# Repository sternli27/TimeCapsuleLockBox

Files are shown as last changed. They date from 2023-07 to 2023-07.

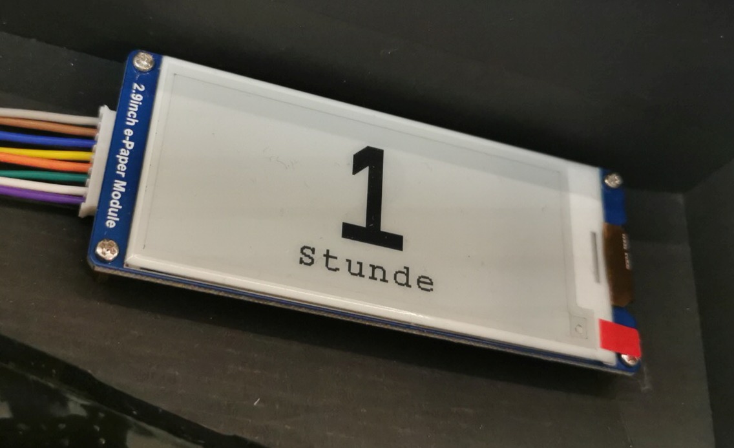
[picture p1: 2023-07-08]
Pictures/epapermodule.jpg

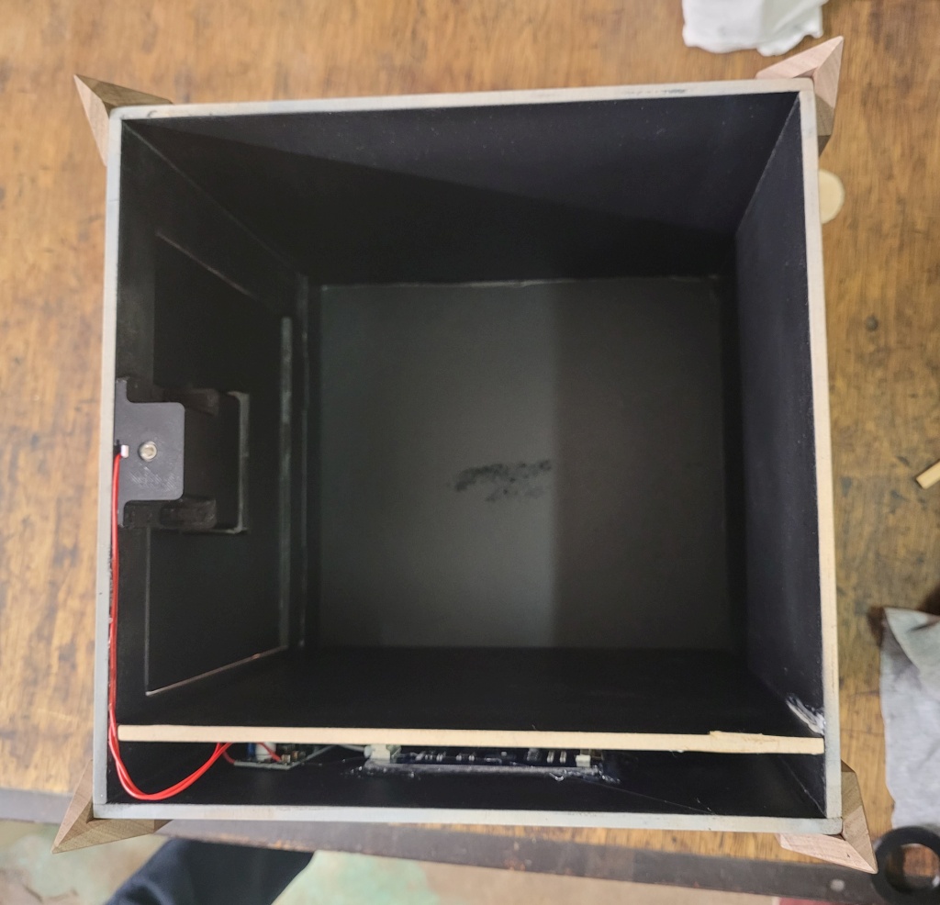
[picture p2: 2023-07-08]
Pictures/20211105_213051.jpg

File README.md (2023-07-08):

# TimeCapsuleLockBox
Here you can find all my project files to build your own DIY Time Capsule Box.

## Purpose
Such a box is perfect as a gift, which opens automatically after one or more years.
The integrated display counts down in days until the box opens on the pre programmed due date. Afterwards, the numbers count up again.
The display updates exactly 1x per day. This takes about 8s. The Teensy spends the rest of the day in deep sleep. Thus, a long battery life is guaranteed.

## Material
- Teensy 3.2
- Crystal 32.768 kHz, 12.5 pF to use the internal RTC on the Teensy 3.2
- Epaper Display Waveshare 2.9" 296 x 128 pixels
- Electromagnet Solenoid 12V 6W (German: Hubmagnet)
- Mosfet N-channel ex. IRLZ34N (low gate threshold voltage)
- Step Up Voltage Boost Converter (only used for solendoid) ex. LM2587
- Energizer Ultimate Lithium AA Batteries

## Electronic connection between the modules
| Teensy Pin  | Connected to |
| --- | --- |
| Vin | Battery Pack 1 positive |
| GND | GND Battery Pack 1+2 + epaper GND (brown)  |
| 3.3V | epaper VCC (grey) |
| VBat | Battery Pack 2 positive (RTC) |
| 7 | epaper BUSY (purple) |
| 8 | epaper RST (white) |
| 9 | epaper DC (green) |
| 10 | epaper CS (orange) |
| 11 | epaper DIN (blue) |
| 12 | |
| 13 | epaper CLK (yellow) |
| 20 | Mosfet Gate |

The Mosfet at pin 20 switches the negative power supply to the StepUp converter.
So the negative supply for the StepUp Converter comes from the Mosfet Drain.
Mosfet source is connected to the GND of battery pack 3.
The positive supply for the StepUp Converter comes from the positive terminal on battery pack 3.
The solenoid is connected to the output of the StepUp Converter.

The solenoid is only actuated for a short time, but it should trip reliably within this short time. For this purpose, set the voltage at the boost converter somewhat higher (e.g. 18V), even if the solenoid is actually designed for 12V.

## Battery Setup
I have had very good experiences with the unfortunately somewhat expensive "Energizer Ultimate Lithium batteries". Don't use cheap batteries, or the project won't last to the end.

For this project I have divided the AA cells into three separate battery packs.
| Battery Pack  | Number of AA cells | Consumer |
| --- | --- | --- |
| 1 | 3 cells in series | Teensy 3.2 Vin 3.6-6.0V (used for daily updates) |
| 2 | 2 cells in series | Teensy 3.2 RTC only |
| 3 | 4 or 6 cells in series  | Boost Converter powering the solenoid |

Caution: Remove the batteries from pack 1 during programming. The batteries have a different voltage than the USB supply.
Or see [here](https://www.pjrc.com/teensy/external_power.html) for other options.

If you need longer battery life, I recommend using 6 batteries with thein battery pack 1. So, 2 groups in parallel and within each group 3 batteries in series.

## CAD
I designed my box in Onshape. You can copy the project and customize it for your needs.
Check it out [here](https://cad.onshape.com/documents/37d5a27263dd0ff057f257a3/w/2627769e2c83fa2f752a5797/e/e0c9090dbd78b67fb374a487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)

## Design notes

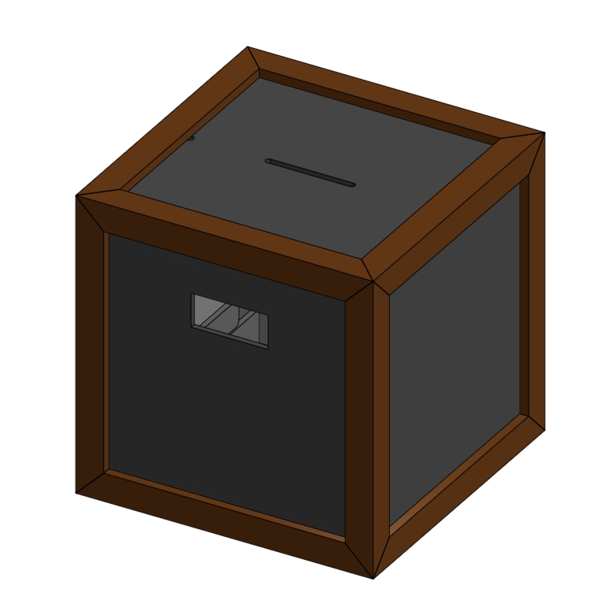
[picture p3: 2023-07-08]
Pictures/CAD.jpg

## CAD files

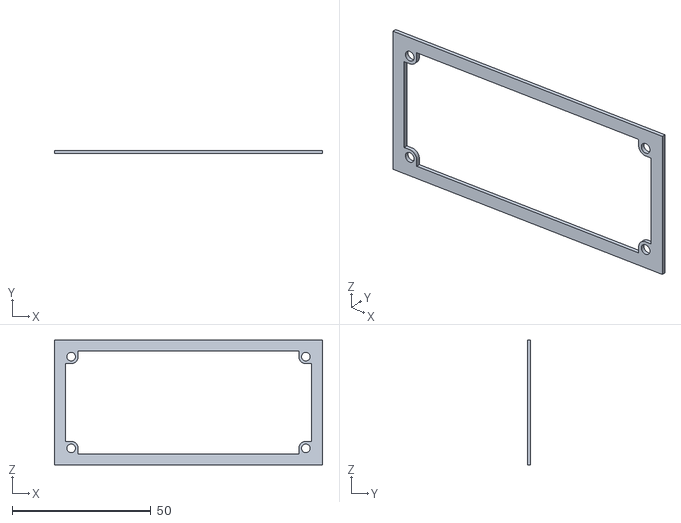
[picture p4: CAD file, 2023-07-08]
3DprintedParts/LockedBox - DisplaySpacer.stl
96.5 x 1.20 x 45.0

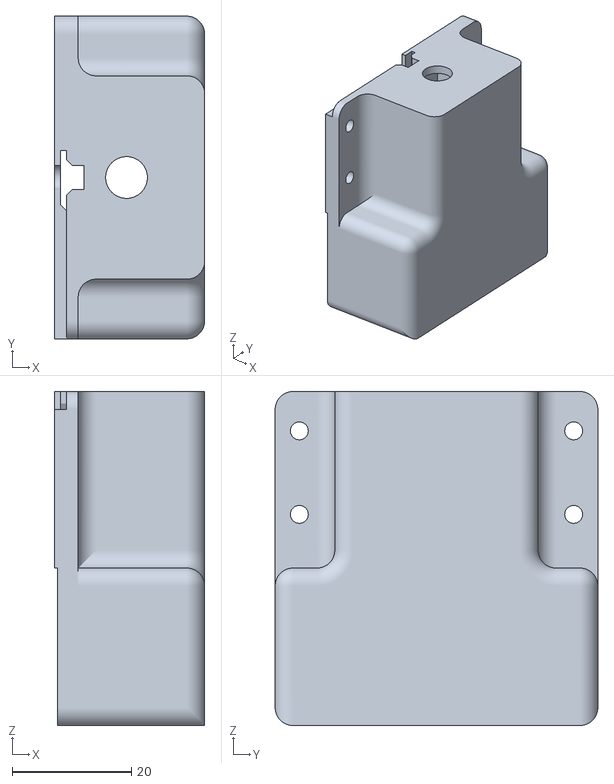
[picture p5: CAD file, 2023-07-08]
3DprintedParts/LockedBox - EMagnetMount.stl
25.2 x 54.1 x 56.0

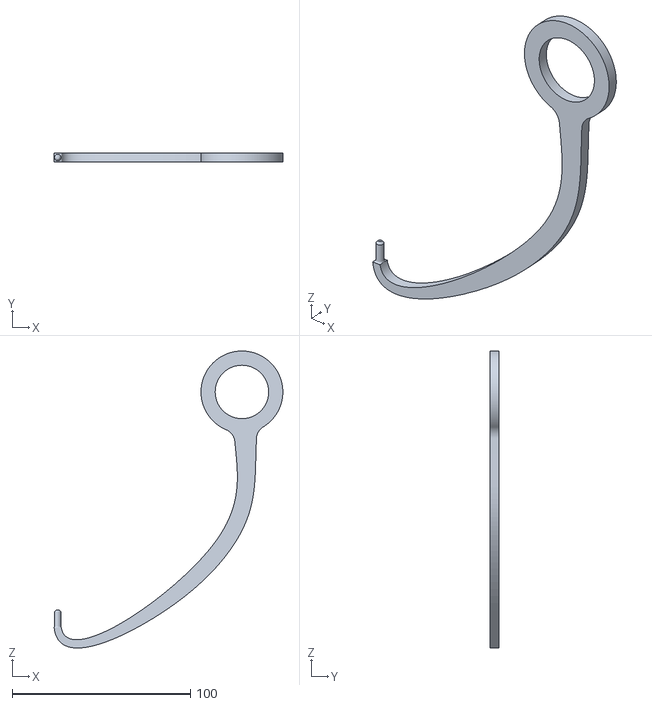
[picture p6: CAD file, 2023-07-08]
3DprintedParts/LockedBox - BackupKey.stl
128.5 x 5.00 x 166.8

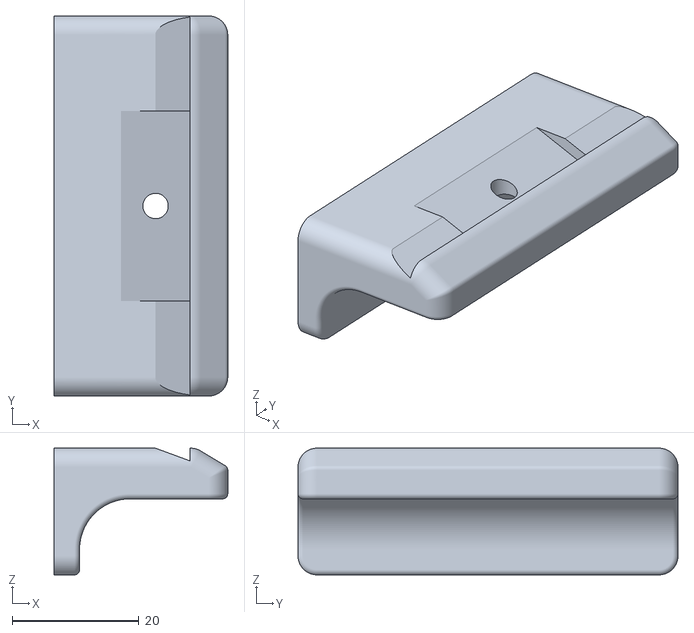
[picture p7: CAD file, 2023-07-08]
3DprintedParts/LockedBox - LockPlate.stl
27.4 x 60.0 x 20.0

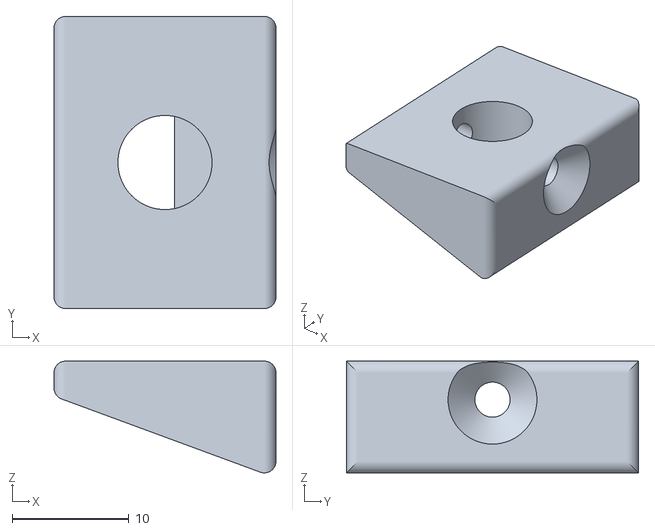
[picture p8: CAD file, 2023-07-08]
3DprintedParts/LockedBox - EMagnetWedge.stl
19.0 x 25.0 x 9.57

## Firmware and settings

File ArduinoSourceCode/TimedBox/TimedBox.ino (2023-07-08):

// Code written for Teensy 3.2 with RTC oscillator. See also https://github.com/PaulStoffregen/Time
// Epaper Display Waveshare 2.9" 296 x 128 pixels
// each update takes about 8s and the current consumed during the update is 41mA
// during standby mode the current consumption is only 0.043mA

//#define DEBUG

#include "Arduino.h"
#include <Snooze.h>
#include <TimeLib.h>

// E-Paper Display
#include <SPI.h>
#include "epd2in9_V2.h"
#include "epdpaint.h"
#include "imagedata.h"

#define COLORED     0
#define UNCOLORED   1

unsigned char image[4800];                                    // buffer big enough for everything
Paint paint(image, 0, 0);                                     // width should be the multiple of 8 
Epd epd;                                                      // allocate Epaper Display

// Load Snooze drivers
SnoozeAlarm alarm;
SnoozeBlock config_teensy32(alarm);

//tmElements_t endTimeElements = {second(), minute(), hour(), weekday(), day(), month(), ( year()-1970) };
#ifdef DEBUG
  const tmElements_t endTimeElements = {0, 16, 14, dowInvalid, 16, 4, CalendarYrToTm(2023) };
#else
  const tmElements_t endTimeElements = {0, 0, 13, dowInvalid, 6, 11, CalendarYrToTm(2021) };
#endif
const time_t endTime = makeTime(endTimeElements);             // unsigned 32bit, overflow expected at 4'294'967'295
enum States { countdownDays, countdownHours, countupDays, countupYears};
States state = countdownDays;

const int doorPin = 20;

#ifndef DEBUG
// undefined reference to _write is an issue on Teensy 3.2 if the program has no usage of any Print class members
// https://forum.pjrc.com/threads/71420-Undefined-reference-to-_write
extern "C" {
  int _write( int handle, char *buf, int count )
  {
    return 0;
      //return Serial.write(buf, count);
  }
}
#endif

void setup() {
  setSyncProvider(getTeensy3Time);                            // set the Time library to use Teensy 3.0's RTC to keep time

  #ifdef DEBUG
    Serial.begin(115200);
    Serial.println("startup");

    Serial.println("DEBUG active");
    /*
    if (Serial.available()) {
      time_t t = processSyncMessage();
      if (t != 0) {
        setTime(t);
        Teensy3Clock.set(t);                                  // set the RTC
      }
    }
    */
    /*
    tmElements_t unixTimeNowElements = {0, 04, 14, dowThursday, 16, 4, ( 2023-1970) };  // second(), minute(), hour(), weekday(), day(), month(), ( year()-1970)
    time_t unixTimeNow = makeTime(unixTimeNowElements);
    setTime(unixTimeNow);
    Teensy3Clock.set(unixTimeNow);
    */
    //setTime(22,41,0,4,11,21);                                 // int hr,int min,int sec,int day, int month, int yr
  #endif

  pinMode(doorPin, OUTPUT);
  digitalWrite(doorPin, LOW);

  if (epd.Init() != 0) {
      #ifdef DEBUG
        Serial.print("e-Paper init failed");
      #endif
      return;
  }
  epd.ClearFrameMemory(0xFF);                                 // bit set = white, bit reset = black
  epd.DisplayFrame();
  epd.ClearFrameMemory(0xFF);                                 // bit set = white, bit reset = black
  epd.DisplayFrame();

}

void loop() {
  setSyncProvider(getTeensy3Time);                            // resync the Time Library with RTC after hibernate
  refreshDisplay();

  // Berechne die Zeit bis zum nächsten Display-Refresh
  uint8_t rhour = (hour(endTime)+24-hour())%24;
  uint8_t rminute = (minute(endTime)+60-minute())%60;
  uint8_t rsecond = (second(endTime)+60-second())%60;
  
  // Set RtcTimer, define next wake up
  #ifdef DEBUG
    Serial.println("sleep");
    delay(5000);
    /*
    if(state == countdownHours)                               // refresh every hour
    {
      alarm.setRtcTimer(0, 0, 20);                            // hour, min, sec
    }
    else {
      alarm.setRtcTimer(0, 0, 40);                            // hour, min, sec
    }
    Snooze.hibernate( config_teensy32 );
    */
  #else
    if(state == countdownHours)                               // refresh every hour
    {
      alarm.setRtcTimer(0, rminute, rsecond);                 // hour, min, sec
    }
    else {
      alarm.setRtcTimer(rhour, rminute, rsecond);             // hour, min, sec
    }
    Snooze.hibernate( config_teensy32 );
  #endif
}

/*
void digitalClockDisplay() {
  // digital clock display of the time
  Serial.print(hour());
  printDigits(minute());
  printDigits(second());
  Serial.print(" ");
  Serial.print(day());
  Serial.print(" ");
  Serial.print(month());
  Serial.print(" ");
  Serial.print(year()); 
  Serial.println(); 
}*/

void refreshDisplay() {
  char tempCharArray[20];
  static uint32_t daysleft = 0;
  static uint32_t hoursleft = 0;
  static uint32_t yearsleft = 0;
  
  epd.Init();                                                 // wake up Epaper from sleep mode
  epd.ClearFrameMemory(0xFF);
  paint.SetRotate(ROTATE_90);
  
  if(day() == 03 && month() == 06)                            // Announce Special Event
  {
    paintText(148, "Happy Birthday", "Name");                 // 148 is the center of the 296 wide display
  }
  else if(day() == 1 && month() == 1)                         // Happy New Year
  {
    paintText(148, "Happy New", "Year");
  }
  else {
    if(now() > endTime && state < countupDays) {              // if endtime is in the past
      state = countupDays;                                    // jump directly to state "countupDays"
    }
    else if(state == countdownDays) {
      daysleft = (uint32_t) (endTime - now()) / SECS_PER_DAY; // calculate daysleft
      if((uint32_t) (endTime - now()) < SECS_PER_DAY / 2 && daysleft > 0) daysleft--;            // round off if less than half a day
      if(daysleft <= 1) {
        state = countdownHours;
      } else {
        paintNumber(148, daysleft, "Tag", "Tage");            // 148 center of 296 wide display
      }
    }

    if(state == countdownHours) {
      hoursleft = (uint32_t) (endTime - now()) / SECS_PER_HOUR;       // remaining seconds divided by seconds and minutes gives remaining hours
      hoursleft += 1;                                         // round up by one, so countdown does not display 0 hours during the last hour.

      if((uint32_t) endTime - now() <= SECS_PER_HOUR / 2)     // if end goal is closer then 30min, open the door
      {
        epd.ClearFrameMemory(0x00);                           // bit set = white, bit reset = black
        epd.DisplayFrame();
        openBox();
        state = countupDays;
      } else {
        paintNumber(148, hoursleft, "Stunde", "Stunden");     // 148 center of 296 wide display
      }
    }

    if(state == countupDays) {
      daysleft = (uint32_t) (now() - endTime) / SECS_PER_DAY;
      if((uint32_t) (now() - endTime) < SECS_PER_DAY / 2 && daysleft > 0) daysleft--;             // round off
      if(daysleft >= 365) {
        state = countupYears;
      } else {
        paintNumber(148, daysleft, "Tag", "Tage");            // 148 center of 296 wide display
      }
    }

    if(state == countupYears) {
      unsigned int yearOfLastAnniversary = year(now()) - 1;   // assume last anniversary was last year
      if(endTimeElements.Month <= month(now()) && endTimeElements.Day <= day(now())) {            // correct value if last anniversary was this year
        yearOfLastAnniversary++;
      }

      tmElements_t lastAnnivElements = {endTimeElements.Second, endTimeElements.Minute, endTimeElements.Hour, dowInvalid, endTimeElements.Day, endTimeElements.Month, (uint8_t) CalendarYrToTm(yearOfLastAnniversary) };
      time_t lastAnnivTime = makeTime(lastAnnivElements);

      yearsleft = (uint32_t) yearOfLastAnniversary - tmYearToCalendar(endTimeElements.Year);
      daysleft = (uint32_t) ((now() - lastAnnivTime) / SECS_PER_DAY);
      //if((uint32_t) (now() - endTime) < SECS_PER_DAY / 2 && daysleft > 0) daysleft--;             // round off

      int yearwidth = getNumberWidth(48, yearsleft);          // font80 is 48px wide per digit, calculate width depending on amount of digits
      int daywidth = getNumberWidth(48, daysleft);
      int emptywidth = 296 - yearwidth - daywidth;            // calculate empty space on 296px wide epaper display
      paintNumber((emptywidth / 4) + (yearwidth / 2), yearsleft, "Jahr", "Jahre");        // paint left number first
      paintNumber((emptywidth * 3 / 4) + yearwidth + (daywidth / 2), daysleft, "Tag", "Tage");
      paintDivider((emptywidth / 2) + yearwidth, 6);          // display 296 x 128

      if(yearsleft == 0) {                                    // go back in case this state got reached to early
        state = countupDays;
      }
    }

    #ifdef DEBUG
      Serial.print("mode: "); Serial.println(state);
      Serial.print("days: "); Serial.println(daysleft);
      Serial.print("hours: "); Serial.println(hoursleft);
      Serial.print("years: "); Serial.println(yearsleft);
      Serial.print("endTime: "); Serial.println(endTime);
      Serial.print("timeNow: "); Serial.println(now());

      // paint date
      paint.SetWidth(16);
      paint.SetHeight(296);
      paint.Clear(COLORED);
      paint.DrawStringAt(125, 2, "DEBUG", &Font16, UNCOLORED); // start 2px lower from the top
      sprintf(tempCharArray, "%02d/%02d/%04d",  day(), month(), year());
      paint.DrawStringAt(0, 2, tempCharArray, &Font16, UNCOLORED);
      sprintf(tempCharArray, "%02d:%02d:%02d",  hour(), minute(), second());
      paint.DrawStringAt(205, 2, tempCharArray, &Font16, UNCOLORED);
      epd.SetFrameMemory(paint.GetImage(), 112, 0, paint.GetWidth(), paint.GetHeight());
    #endif
  }

  epd.DisplayFrame();
  epd.Sleep();                                                // put Epaper in sleep mode
  delay(1);
  digitalWrite(RST_PIN, LOW);                                 // shut down powersupply inside epaper display
  
  return;
}

int getNumberWidth(int charwidth, int number) {
  if(number < 0) { return 0; }
  int width = 1;                                              // count digits
  if(number > 10) width++;
  if(number > 100) width++;
  if(number > 1000) width++;

  width *= charwidth;                                         // get width in pixels
  if(width < 80) {                                            // min width = 5 small chars with each 16px width for subtitle
    width = 80;
  }
  return width;
}

void paintNumber(int center, int number, const char* unit1, const char* unitx) {
  if(center < 0 || number < 0 || number > 999) { return; }

  char tempCharArray[14];
  int numberstart = center - 72;                              // shift number in y direction (to the right)
  if(number < 100) numberstart = center - 48;
  if(number < 10) numberstart = center - 24;
  
  paint.SetWidth(80);
  paint.SetHeight(144);                                       // allows up to 3 digits (each 48px)
  sprintf(tempCharArray, "%d", number);
  paint.Clear(UNCOLORED);
  paint.DrawStringAt(0, 0, tempCharArray, &Font80, COLORED);
  epd.SetFrameMemory(paint.GetImage(), 32, numberstart, paint.GetWidth(), paint.GetHeight());
  
  int textwidth = strlen(number == 1 ? unit1 : unitx) * 17;   // each char is approx 16.5px wide
  paint.SetWidth(24);
  paint.SetHeight(textwidth);                                 // width and height is flipped, because of display rotation
  paint.Clear(UNCOLORED);
  paint.DrawStringAt(0, 0, number == 1 ? unit1 : unitx, &Font24, COLORED);
  epd.SetFrameMemory(paint.GetImage(), 0, center - (textwidth / 2), paint.GetWidth(), paint.GetHeight());
}

void paintText(int center, const char* upperText, const char* lowerText) {
  if(center < 0) { return; }

  int textwidth = strlen(upperText) * 17;                     // each char is approx 16.5px wide
  paint.SetWidth(24);
  paint.SetHeight(textwidth);                                 // allows up to 3 digits (each 48px)
  paint.Clear(UNCOLORED);
  paint.DrawStringAt(0, 0, upperText, &Font24, COLORED);
  epd.SetFrameMemory(paint.GetImage(), 88, center - (textwidth / 2), paint.GetWidth(), paint.GetHeight());
  
  textwidth = strlen(lowerText) * 41;                         // each char is approx 41px wide
  paint.SetWidth(64);
  paint.SetHeight(textwidth);                                 // width and height is flipped, because of display rotation
  paint.Clear(UNCOLORED);
  paint.DrawStringAt(0, 0, lowerText, &Font64, COLORED);
  epd.SetFrameMemory(paint.GetImage(), 16, center - (textwidth / 2), paint.GetWidth(), paint.GetHeight());
}

void paintDivider(int center, int width) {
  paint.SetWidth(128);
  paint.SetHeight(width);
  paint.Clear(UNCOLORED);
  paint.DrawFilledRectangle(0, 6, width, 128, COLORED);       // start line 6px below top, because of mechanical situation
  epd.SetFrameMemory(paint.GetImage(), 0, center - (width/2), paint.GetWidth(), paint.GetHeight());
}

void openBox() {
  pinMode(doorPin, OUTPUT);
  digitalWrite(doorPin, HIGH);
  delay(1000);
  digitalWrite(doorPin, LOW);
  delay(4000);
  digitalWrite(doorPin, HIGH);
  delay(1000);
  digitalWrite(doorPin, LOW);
}

time_t getTeensy3Time()
{
  return Teensy3Clock.get();
}

#ifdef DEBUG                                                  // code to process time sync messages from the serial port
  unsigned long processSyncMessage() {
    unsigned long pctime = 0L;
    const unsigned long DEFAULT_TIME = 1357041600;            // Jan 1 2013 
  
    if(Serial.find("T")) {                                    // Header tag for serial time sync message
       pctime = Serial.parseInt();
       return pctime;
       if( pctime < DEFAULT_TIME) {                           // check the value is a valid time (greater than Jan 1 2013)
         pctime = 0L;                                         // return 0 to indicate that the time is not valid
       }
    }
    return pctime;
  }
  
  void printDigits(int digits) {                              // utility function for digital clock display: prints preceding colon and leading 0
    Serial.print(":");
    if(digits < 10)
      Serial.print('0');
    Serial.print(digits);
  }
#endif

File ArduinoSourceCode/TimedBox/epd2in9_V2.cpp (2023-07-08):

/**
 *  @filename   :   epd2in9_V2.cpp
 *  @brief      :   Implements for e-paper library
 *  @author     :  
 *
 *  Copyright (C) Waveshare     Nov 9 2020
 *
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
 * THE SOFTWARE IS PROVIDED "AS IS", WITHOUT WARRANTY OF ANY KIND, EXPRESS OR
 * IMPLIED, INCLUDING BUT NOT LIMITED TO THE WARRANTIES OF MERCHANTABILITY,
 * FITNESS OR A PARTICULAR PURPOSE AND NONINFRINGEMENT. IN NO EVENT SHALL THE
 * AUTHORS OR COPYRIGHT HOLDERS BE LIABLE FOR ANY CLAIM, DAMAGES OR OTHER
 * LIABILITY WHETHER IN AN ACTION OF CONTRACT, TORT OR OTHERWISE, ARISING FROM,
 * OUT OF OR IN CONNECTION WITH THE SOFTWARE OR THE USE OR OTHER DEALINGS IN
 * THE SOFTWARE.
 */

#include <stdlib.h>
#include "epd2in9_V2.h"

unsigned char _WF_PARTIAL_2IN9[159] =
{
0x0,0x40,0x0,0x0,0x0,0x0,0x0,0x0,0x0,0x0,0x0,0x0,
0x80,0x80,0x0,0x0,0x0,0x0,0x0,0x0,0x0,0x0,0x0,0x0,
0x40,0x40,0x0,0x0,0x0,0x0,0x0,0x0,0x0,0x0,0x0,0x0,
0x0,0x80,0x0,0x0,0x0,0x0,0x0,0x0,0x0,0x0,0x0,0x0,
0x0,0x0,0x0,0x0,0x0,0x0,0x0,0x0,0x0,0x0,0x0,0x0,
0x0A,0x0,0x0,0x0,0x0,0x0,0x2,  
0x1,0x0,0x0,0x0,0x0,0x0,0x0,
0x1,0x0,0x0,0x0,0x0,0x0,0x0,
0x0,0x0,0x0,0x0,0x0,0x0,0x0,
0x0,0x0,0x0,0x0,0x0,0x0,0x0,
0x0,0x0,0x0,0x0,0x0,0x0,0x0,
0x0,0x0,0x0,0x0,0x0,0x0,0x0,
0x0,0x0,0x0,0x0,0x0,0x0,0x0,
0x0,0x0,0x0,0x0,0x0,0x0,0x0,
0x0,0x0,0x0,0x0,0x0,0x0,0x0,
0x0,0x0,0x0,0x0,0x0,0x0,0x0,
0x0,0x0,0x0,0x0,0x0,0x0,0x0,
0x22,0x22,0x22,0x22,0x22,0x22,0x0,0x0,0x0,
0x22,0x17,0x41,0xB0,0x32,0x36,
};

unsigned char WS_20_30[159] =
{											
0x80,	0x66,	0x0,	0x0,	0x0,	0x0,	0x0,	0x0,	0x40,	0x0,	0x0,	0x0,
0x10,	0x66,	0x0,	0x0,	0x0,	0x0,	0x0,	0x0,	0x20,	0x0,	0x0,	0x0,
0x80,	0x66,	0x0,	0x0,	0x0,	0x0,	0x0,	0x0,	0x40,	0x0,	0x0,	0x0,
0x10,	0x66,	0x0,	0x0,	0x0,	0x0,	0x0,	0x0,	0x20,	0x0,	0x0,	0x0,
0x0,	0x0,	0x0,	0x0,	0x0,	0x0,	0x0,	0x0,	0x0,	0x0,	0x0,	0x0,
0x14,	0x8,	0x0,	0x0,	0x0,	0x0,	0x1,					
0xA,	0xA,	0x0,	0xA,	0xA,	0x0,	0x1,					
0x0,	0x0,	0x0,	0x0,	0x0,	0x0,	0x0,					
0x0,	0x0,	0x0,	0x0,	0x0,	0x0,	0x0,					
0x0,	0x0,	0x0,	0x0,	0x0,	0x0,	0x0,					
0x0,	0x0,	0x0,	0x0,	0x0,	0x0,	0x0,					
0x0,	0x0,	0x0,	0x0,	0x0,	0x0,	0x0,					
0x0,	0x0,	0x0,	0x0,	0x0,	0x0,	0x0,					
0x14,	0x8,	0x0,	0x1,	0x0,	0x0,	0x1,					
0x0,	0x0,	0x0,	0x0,	0x0,	0x0,	0x1,					
0x0,	0x0,	0x0,	0x0,	0x0,	0x0,	0x0,					
0x0,	0x0,	0x0,	0x0,	0x0,	0x0,	0x0,					
0x44,	0x44,	0x44,	0x44,	0x44,	0x44,	0x0,	0x0,	0x0,			
0x22,	0x17,	0x41,	0x0,	0x32,	0x36
};	

Epd::~Epd() {
};

Epd::Epd() {
    reset_pin = RST_PIN;
    dc_pin = DC_PIN;
    cs_pin = CS_PIN;
    busy_pin = BUSY_PIN;
    width = EPD_WIDTH;
    height = EPD_HEIGHT;
};

int Epd::Init() {
    /* this calls the peripheral hardware interface, see epdif */
    if (IfInit() != 0) {
        return -1;
    }
	
	Reset();
	
    /* EPD hardware init start */
	WaitUntilIdle();   
	SendCommand(0x12);  //SWRESET
	WaitUntilIdle();   
	
	SendCommand(0x01); //Driver output control      
	SendData(0x27);
	SendData(0x01);
	SendData(0x00);
	
	SendCommand(0x11); //data entry mode       
	SendData(0x03);

	SetMemoryArea(0, 0, width-1, height-1);

	SendCommand(0x21); //  Display update control
	SendData(0x00);
	SendData(0x80);	

	SetMemoryPointer(0, 0);
	WaitUntilIdle();

    SetLut_by_host(WS_20_30);
    /* EPD hardware init end */
    return 0;
}

/**
 *  @brief: basic function for sending commands
 */
void Epd::SendCommand(unsigned char command) {
    DigitalWrite(dc_pin, LOW);
    DigitalWrite(cs_pin, LOW);
    SpiTransfer(command);
    DigitalWrite(cs_pin, HIGH);
}

/**
 *  @brief: basic function for sending data
 */
void Epd::SendData(unsigned char data) {
    DigitalWrite(dc_pin, HIGH);
    DigitalWrite(cs_pin, LOW);
    SpiTransfer(data);
    DigitalWrite(cs_pin, HIGH);
}

/**
 *  @brief: Wait until the busy_pin goes LOW
 */
void Epd::WaitUntilIdle(void) {
	while(1) {	 //=1 BUSY
		if(DigitalRead(busy_pin)==LOW) 
			break;
		DelayMs(5);
	}
	DelayMs(5);
}

/**
 *  @brief: module reset.
 *          often used to awaken the module in deep sleep,
 *          see Epd::Sleep();
 */
void Epd::Reset(void) {
    DigitalWrite(reset_pin, HIGH);
    DelayMs(20);  
    DigitalWrite(reset_pin, LOW);                //module reset    
    DelayMs(5);
    DigitalWrite(reset_pin, HIGH); 
    DelayMs(20);  
}

/**
 *  @brief: put an image buffer to the frame memory.
 *          this won't update the display.
 */
void Epd::SetFrameMemory(
    const unsigned char* image_buffer,
    int x,
    int y,
    int image_width,
    int image_height
) {
    int x_end;
    int y_end;

    if (
        image_buffer == NULL ||
        x < 0 || image_width < 0 ||
        y < 0 || image_height < 0
    ) {
        return;
    }
    /* x point must be the multiple of 8 or the last 3 bits will be ignored */
    x &= 0xF8;
    image_width &= 0xF8;
    if (x + image_width >= (int) this->width) {
        x_end = this->width - 1;
    } else {
        x_end = x + image_width - 1;
    }
    if (y + image_height >= (int) this->height) {
        y_end = this->height - 1;
    } else {
        y_end = y + image_height - 1;
    }
    SetMemoryArea(x, y, x_end, y_end);
    SetMemoryPointer(x, y);
    SendCommand(0x24);
    /* send the image data */
    for (int j = 0; j < y_end - y + 1; j++) {
        for (int i = 0; i < (x_end - x + 1) / 8; i++) {
            SendData(image_buffer[i + j * (image_width / 8)]);
        }
    }
}
void Epd::SetFrameMemory_Partial(
    const unsigned char* image_buffer,
    int x,
    int y,
    int image_width,
    int image_height
) {
    int x_end;
    int y_end;

    if (
        image_buffer == NULL ||
        x < 0 || image_width < 0 ||
        y < 0 || image_height < 0
    ) {
        return;
    }
    /* x point must be the multiple of 8 or the last 3 bits will be ignored */
    x &= 0xF8;
    image_width &= 0xF8;
    if (x + image_width >= (int) this->width) {
        x_end = this->width - 1;
    } else {
        x_end = x + image_width - 1;
    }
    if (y + image_height >= (int) this->height) {
        y_end = this->height - 1;
    } else {
        y_end = y + image_height - 1;
    }

    DigitalWrite(reset_pin, LOW);
    DelayMs(2);
    DigitalWrite(reset_pin, HIGH);
    DelayMs(2);
	
	SetLut(_WF_PARTIAL_2IN9);
	SendCommand(0x37); 
	SendData(0x00);  
	SendData(0x00);  
	SendData(0x00);  
	SendData(0x00); 
	SendData(0x00);  	
	SendData(0x40);  
	SendData(0x00);  
	SendData(0x00);   
	SendData(0x00);  
	SendData(0x00);

	SendCommand(0x3C); //BorderWavefrom
	SendData(0x80);	

	SendCommand(0x22); 
	SendData(0xC0);   
	SendCommand(0x20); 
	WaitUntilIdle();  
	
    SetMemoryArea(x, y, x_end, y_end);
    SetMemoryPointer(x, y);
    SendCommand(0x24);
    /* send the image data */
    for (int j = 0; j < y_end - y + 1; j++) {
        for (int i = 0; i < (x_end - x + 1) / 8; i++) {
            SendData(image_buffer[i + j * (image_width / 8)]);
        }
    }
}
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
